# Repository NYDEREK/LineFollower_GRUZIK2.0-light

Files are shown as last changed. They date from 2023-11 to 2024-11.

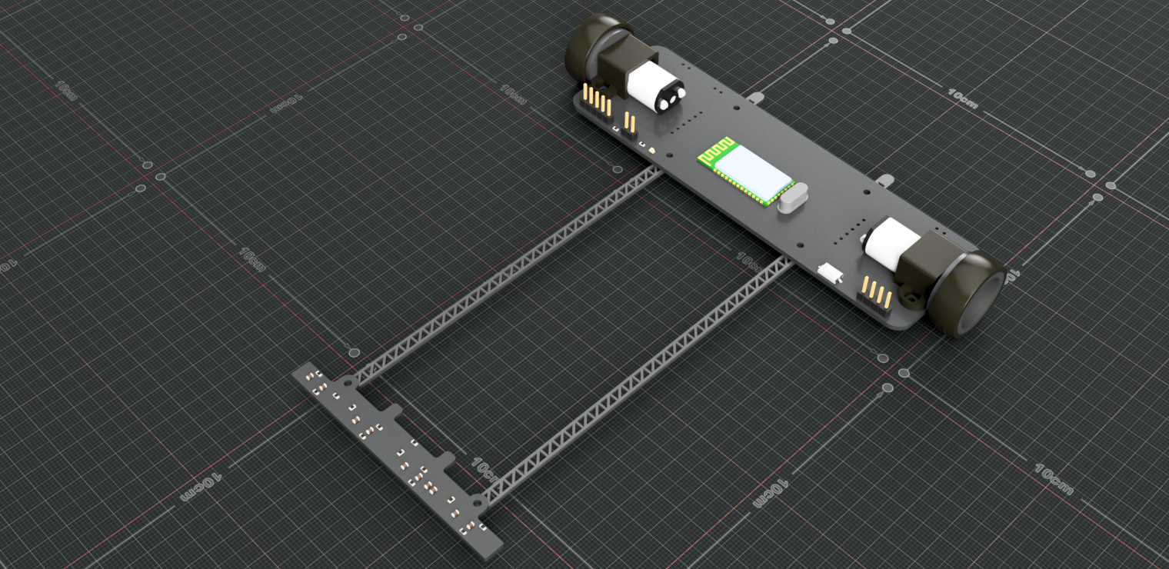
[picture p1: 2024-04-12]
Gruzik2.0-light/Hardware/CAD_Renders/Gruzik2.0_Sensor v7.png

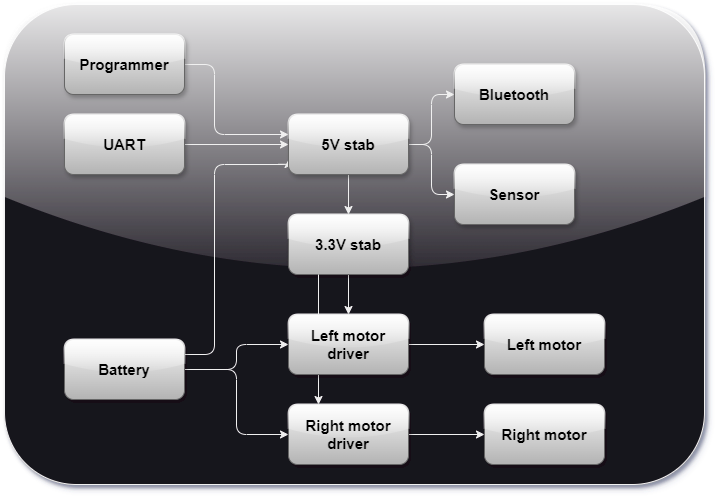
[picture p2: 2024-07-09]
Gruzik2.0-light/Hardware/SubSystem/Power_schemat.png

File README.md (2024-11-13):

<h1 align="center">GRUZIK2.0: Line Follower Robot</h1>

<div align="center">

   

<i>Loved the project? Please consider giving a Star ⭐️</i>

</div>

> **GRUZIK2.0 is a lightweight construction (62g) designed for the "Line Follower Light" competition. The robot features Bluetooth communication with a smartphone app and uses a digital sensor instead of analog.**

<div align="center">
  
</div>

<div align="center">
  
  
</div>

## Hardware

> **The simple lightweight construction (74g) allows the robot to achieve high speed on the track.**
> **PCBs were designed in KiCAD 7.0 and manufactured by JLCPCB. The rims were 3D printed with PETG for Kyosho "Mini Z" tires.**
> **The light dualsky 150mAh battery provides enough current (max 30C) without adding too much weight (10g).**
> **The Pololu 2211 motor (10:1) with max current 1.6A per one requires the use of two separate TB6612FNG motor drivers with connected channels (max 2A per driver).**
> **The HC-05 Bluetooth module gives communication range up to 10m.**
> **The fast ARM microcontroller STM32F103C8T6 (max 72MHz) provides a lot of software capabilities.**

- uC - STM32F103C8T6
- drivers - TB6612FNG
- sensor - 8x KTIR0711S
- battery - 150mAh LiPo dualsky
- wheels - Kyosho Mini Z
- motors - Pololu 2211
- Bluetooth - HC-05

<div align="center">
  
  
</div>

## 📱Bluetooth Apps 📱

> **Thease are simple Bluetooth apps created with MIT App Inventor. Spps start and stop the robot. The Modes pad is responsible for quickly adapting the speed and accuracy of the robot to the route using modes, and the application also displays the battery charge status. Second app is mainly for tweaking PID settings it allows you to change any parameter in seconds**

<div align="center">
  
  
</div>

## Credits

> <i>**I implemented the PD controller in my project, drawing inspiration from Bilal Kabas' repository available at - https://github.com/sametoguten/STM32-Line-Follower-with-PID with MIT License - [MIT License](LICENSE)**<i>

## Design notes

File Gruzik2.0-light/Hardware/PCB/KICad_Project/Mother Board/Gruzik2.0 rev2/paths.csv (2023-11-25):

Kod sieci | Nazwa sieci | Liczba pól lut | Liczba przelotek | Długość przelotki | Długość ścieżki | Długość rdzenia | Długość Sieci | F.Cu | B.Cu
001 | GND | 44 | 0 | 0,0000 mm | 0,0000 mm | 0,0000 mm | 0,0000 mm | 0,0000 mm | 0,0000 mm
002 | /BOOT0 | 3 | 0 | 0,0000 mm | 0,0000 mm | 0,0000 mm | 0,0000 mm | 0,0000 mm | 0,0000 mm
003 | +3.3V | 15 | 0 | 0,0000 mm | 0,0000 mm | 0,0000 mm | 0,0000 mm | 0,0000 mm | 0,0000 mm
004 | /HSE_OUT | 3 | 2 | 3,0900 mm | 22,3316 mm | 0,0000 mm | 25,4216 mm | 9,0906 mm | 13,2411 mm
005 | /HSE_IN | 3 | 2 | 3,0900 mm | 21,1634 mm | 0,0000 mm | 24,2534 mm | 9,8856 mm | 11,2778 mm
006 | +3.3VA | 4 | 0 | 0,0000 mm | 0,0000 mm | 0,0000 mm | 0,0000 mm | 0,0000 mm | 0,0000 mm
007 | VDC | 10 | 0 | 0,0000 mm | 0,0000 mm | 0,0000 mm | 0,0000 mm | 0,0000 mm | 0,0000 mm
008 | +5V | 14 | 0 | 0,0000 mm | 0,0000 mm | 0,0000 mm | 0,0000 mm | 0,0000 mm | 0,0000 mm
009 | Motor_R | 7 | 0 | 0,0000 mm | 0,0000 mm | 0,0000 mm | 0,0000 mm | 0,0000 mm | 0,0000 mm
010 | Motor_L | 7 | 0 | 0,0000 mm | 0,0000 mm | 0,0000 mm | 0,0000 mm | 0,0000 mm | 0,0000 mm
011 | Net-(D1-K) | 2 | 0 | 0,0000 mm | 0,0000 mm | 0,0000 mm | 0,0000 mm | 0,0000 mm | 0,0000 mm
012 | PC13 | 2 | 0 | 0,0000 mm | 0,0000 mm | 0,0000 mm | 0,0000 mm | 0,0000 mm | 0,0000 mm
013 | PB0 | 2 | 0 | 0,0000 mm | 0,0000 mm | 0,0000 mm | 0,0000 mm | 0,0000 mm | 0,0000 mm
014 | PA7 | 2 | 0 | 0,0000 mm | 0,0000 mm | 0,0000 mm | 0,0000 mm | 0,0000 mm | 0,0000 mm
015 | PA6 | 2 | 0 | 0,0000 mm | 0,0000 mm | 0,0000 mm | 0,0000 mm | 0,0000 mm | 0,0000 mm
016 | PA5 | 2 | 0 | 0,0000 mm | 0,0000 mm | 0,0000 mm | 0,0000 mm | 0,0000 mm | 0,0000 mm
017 | PA4 | 2 | 0 | 0,0000 mm | 0,0000 mm | 0,0000 mm | 0,0000 mm | 0,0000 mm | 0,0000 mm
018 | PA3 | 2 | 0 | 0,0000 mm | 0,0000 mm | 0,0000 mm | 0,0000 mm | 0,0000 mm | 0,0000 mm
019 | PA2 | 2 | 0 | 0,0000 mm | 0,0000 mm | 0,0000 mm | 0,0000 mm | 0,0000 mm | 0,0000 mm
020 | PA1 | 2 | 0 | 0,0000 mm | 0,0000 mm | 0,0000 mm | 0,0000 mm | 0,0000 mm | 0,0000 mm
021 | PA0 | 2 | 0 | 0,0000 mm | 0,0000 mm | 0,0000 mm | 0,0000 mm | 0,0000 mm | 0,0000 mm
022 | Net-(Motor-STAB-Battery-L1-B) | 2 | 0 | 0,0000 mm | 0,0000 mm | 0,0000 mm | 0,0000 mm | 0,0000 mm | 0,0000 mm
023 | Net-(Motor-STAB-Battery-R1-B) | 2 | 0 | 0,0000 mm | 0,0000 mm | 0,0000 mm | 0,0000 mm | 0,0000 mm | 0,0000 mm
024 | Net-(Motor_L1-Pin_1) | 5 | 0 | 0,0000 mm | 0,0000 mm | 0,0000 mm | 0,0000 mm | 0,0000 mm | 0,0000 mm
025 | Net-(Motor_L1-Pin_2) | 5 | 0 | 0,0000 mm | 0,0000 mm | 0,0000 mm | 0,0000 mm | 0,0000 mm | 0,0000 mm
026 | Net-(Motor_R1-Pin_1) | 5 | 0 | 0,0000 mm | 0,0000 mm | 0,0000 mm | 0,0000 mm | 0,0000 mm | 0,0000 mm
027 | Net-(Motor_R1-Pin_2) | 5 | 0 | 0,0000 mm | 0,0000 mm | 0,0000 mm | 0,0000 mm | 0,0000 mm | 0,0000 mm
028 | SWDIO | 2 | 0 | 0,0000 mm | 0,0000 mm | 0,0000 mm | 0,0000 mm | 0,0000 mm | 0,0000 mm
029 | SWCLK | 2 | 0 | 0,0000 mm | 0,0000 mm | 0,0000 mm | 0,0000 mm | 0,0000 mm | 0,0000 mm
030 | PB1 | 3 | 0 | 0,0000 mm | 0,0000 mm | 0,0000 mm | 0,0000 mm | 0,0000 mm | 0,0000 mm
031 | Net-(SW_Reset1-B) | 2 | 0 | 0,0000 mm | 0,0000 mm | 0,0000 mm | 0,0000 mm | 0,0000 mm | 0,0000 mm
032 | PC14 | 1 | 0 | 0,0000 mm | 0,0000 mm | 0,0000 mm | 0,0000 mm | 0,0000 mm | 0,0000 mm
033 | PC15 | 1 | 0 | 0,0000 mm | 0,0000 mm | 0,0000 mm | 0,0000 mm | 0,0000 mm | 0,0000 mm
034 | PB2 | 1 | 0 | 0,0000 mm | 0,0000 mm | 0,0000 mm | 0,0000 mm | 0,0000 mm | 0,0000 mm
035 | PB10 | 3 | 0 | 0,0000 mm | 0,0000 mm | 0,0000 mm | 0,0000 mm | 0,0000 mm | 0,0000 mm
036 | PB11 | 3 | 0 | 0,0000 mm | 0,0000 mm | 0,0000 mm | 0,0000 mm | 0,0000 mm | 0,0000 mm
037 | PB12 | 1 | 0 | 0,0000 mm | 0,0000 mm | 0,0000 mm | 0,0000 mm | 0,0000 mm | 0,0000 mm
038 | PB13 | 1 | 0 | 0,0000 mm | 0,0000 mm | 0,0000 mm | 0,0000 mm | 0,0000 mm | 0,0000 mm
039 | PB14 | 3 | 0 | 0,0000 mm | 0,0000 mm | 0,0000 mm | 0,0000 mm | 0,0000 mm | 0,0000 mm
040 | PB15 | 3 | 0 | 0,0000 mm | 0,0000 mm | 0,0000 mm | 0,0000 mm | 0,0000 mm | 0,0000 mm
041 | PA8 | 1 | 0 | 0,0000 mm | 0,0000 mm | 0,0000 mm | 0,0000 mm | 0,0000 mm | 0,0000 mm
042 | PA9 | 1 | 0 | 0,0000 mm | 0,0000 mm | 0,0000 mm | 0,0000 mm | 0,0000 mm | 0,0000 mm
043 | PA10 | 1 | 0 | 0,0000 mm | 0,0000 mm | 0,0000 mm | 0,0000 mm | 0,0000 mm | 0,0000 mm
044 | PA11 | 1 | 0 | 0,0000 mm | 0,0000 mm | 0,0000 mm | 0,0000 mm | 0,0000 mm | 0,0000 mm
045 | PA12 | 1 | 0 | 0,0000 mm | 0,0000 mm | 0,0000 mm | 0,0000 mm | 0,0000 mm | 0,0000 mm
046 | PA15 | 1 | 0 | 0,0000 mm | 0,0000 mm | 0,0000 mm | 0,0000 mm | 0,0000 mm | 0,0000 mm
047 | SWO | 1 | 0 | 0,0000 mm | 0,0000 mm | 0,0000 mm | 0,0000 mm | 0,0000 mm | 0,0000 mm
048 | PB4 | 3 | 0 | 0,0000 mm | 0,0000 mm | 0,0000 mm | 0,0000 mm | 0,0000 mm | 0,0000 mm
049 | PB5 | 3 | 0 | 0,0000 mm | 0,0000 mm | 0,0000 mm | 0,0000 mm | 0,0000 mm | 0,0000 mm
050 | PB6 | 3 | 0 | 0,0000 mm | 0,0000 mm | 0,0000 mm | 0,0000 mm | 0,0000 mm | 0,0000 mm
051 | PB7 | 3 | 0 | 0,0000 mm | 0,0000 mm | 0,0000 mm | 0,0000 mm | 0,0000 mm | 0,0000 mm
052 | PB8 | 1 | 0 | 0,0000 mm | 0,0000 mm | 0,0000 mm | 0,0000 mm | 0,0000 mm | 0,0000 mm
053 | PB9 | 3 | 0 | 0,0000 mm | 0,0000 mm | 0,0000 mm | 0,0000 mm | 0,0000 mm | 0,0000 mm
056 | Net-(U4-PGND1-Pad3) | 4 | 0 | 0,0000 mm | 0,0000 mm | 0,0000 mm | 0,0000 mm | 0,0000 mm | 0,0000 mm
057 | Net-(U5-PGND1-Pad3) | 4 | 0 | 0,0000 mm | 0,0000 mm | 0,0000 mm | 0,0000 mm | 0,0000 mm | 0,0000 mm

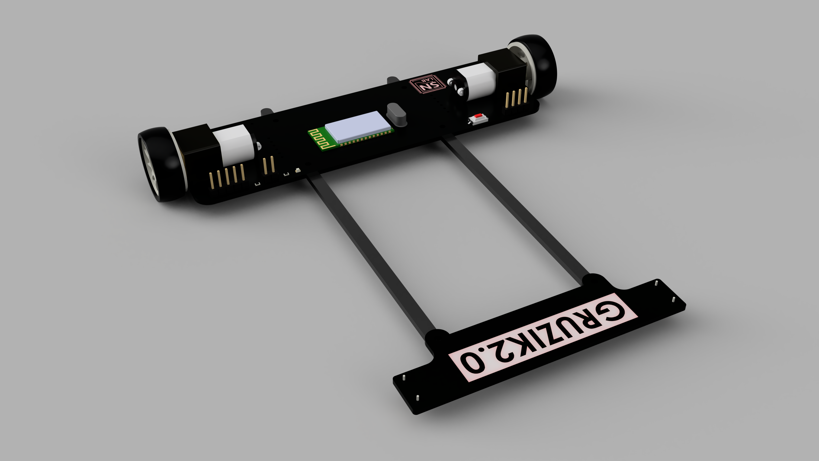
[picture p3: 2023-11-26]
Gruzik2.0-light/Hardware/CAD_Renders/26.11.2023r-First_render.PNG

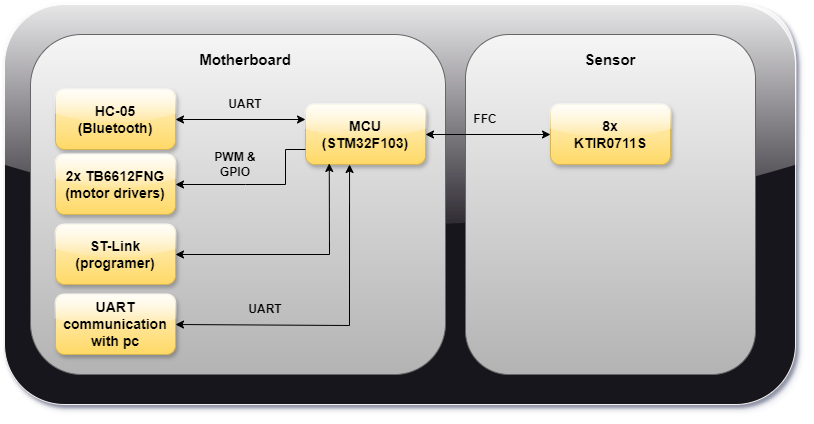
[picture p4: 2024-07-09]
Gruzik2.0-light/Hardware/SubSystem/signals.png

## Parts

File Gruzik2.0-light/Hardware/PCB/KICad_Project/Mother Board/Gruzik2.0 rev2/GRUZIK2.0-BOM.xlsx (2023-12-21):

Nr | Reference | Qty | Val | Footprint | SOURCE
 | MAIN BOARD
1 | BOOT1 | 1 | - | Conn_PinHeader_2.54mm_1x02 | HOME
2 | C1 | 1 | 4u7 | SMD 0603 1608metric | LCSC
3 | C2,C4,C6,C7,C9,C20 | 6 | 100n | SMD 0603 1608metric | LCSC
4 | C3,C5 | 2 | 20p | SMD 0603 1608metric | LCSC
5 | C8 | 1 | 1u | SMD 0603 1608metric | LCSC
6 | C10,C12,C16,C19 | 4 | 10u | SMD 0603 1608metric | LCSC
7 | C11,C13 | 2 | 33u -> 22u | SMD 0603 1608metric | LCSC
8 | C14,C15,C17,C18 | 5 | 0.1u | SMD 0603 1608metric | LCSC
9 | D1 | 1 | Blue | LED_0603_1608metric | LCSC
10 | Conn-FFC | 2 |  | 01x16-1.0mm grid -Druciarstwo z footprintem | LCSC
11 | L1 | 1 | 27n | SMD 0603 1608metric | LCSC
12 | R1 | 1 | 10k | SMD 0603 1608metric | LCSC
13 | R2 | 1 | 20k | SMD 0603 1608metric | LCSC
14 | R3 | 1 | 510R | SMD 0603 1608metric | LCSC
15 | R4 | 1 | 33k | SMD 0603 1608metric | LCSC
16 | RESET-button | 1 | - | Button_Switch_SMD:SW_SPST_CK_RS282G05A | LCSC
17 | STM32F103C8T6 | 1 | - | LQFP-48_7x7mm_P0.5mm | LCSC
18 | LM1117MP-3,3V | 1 | - | TO_SOT_SMD:SOT-223-3_TabPin2 | LCSC
19 | LM1117MP-5V | 1 | - | TO_SOT_SMD:SOT-223-3_TabPin2 | LCSC
20 | TB6612FNG | 2 |  | SSOP-24_5.3x8.2mm_P0.65mm | LCSC
21 | HC-05 | 1 |  |  | HOME
22 | Crystal | 1 | 8Mhz | Crystal_HC49-4H_Vertical | LCSC
 | SENSOR
23 | C2 | 1 | 1.0u | SMD 0603 1608metric | LCSC
24 | C3, C4, C5, C6, C7, C8, C9, C10 | 8 | 10n | SMD 0603 1608metric | LCSC
25 | KTIR0711S | 8 | - | - | LCSC
26 | Q1-NMOS | 1 |  | SOT23 | LCSC
27 | R1,R4,R7,R10 | 4 | 39 | SMD 0603 1608metric | LCSC
28 | R2,R3,R5,R7,R11,R12 | 8 | 220 | SMD 0603 1608metric | LCSC
29 | R12,R14 | 2 | 47 | SMD 0603 1608metric | LCSC
30 | R15 | 1 | 47K | SMD 0603 1608metric | LCSC

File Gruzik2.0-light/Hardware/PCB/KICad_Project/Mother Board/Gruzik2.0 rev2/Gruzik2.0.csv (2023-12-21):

# | Reference | Qty | Value | Footprint | DNP
1 | BOOT1 | 1 | Conn_01x02_Pin | Connector_PinHeader_2.54mm:PinHeader_1x02_P2.54mm_Vertical
2 | C1 | 1 | 4u7 | Capacitor_SMD:C_0603_1608Metric
3 | C2, C4, C6, C7, C9, C20 | 6 | 100n | Capacitor_SMD:C_0603_1608Metric
4 | C3, C5 | 2 | 20p | Capacitor_SMD:C_0603_1608Metric
5 | C8 | 1 | 1u | Capacitor_SMD:C_0603_1608Metric
6 | C10, C12, C16, C19 | 4 | 10u | Capacitor_SMD:C_0603_1608Metric
7 | C11, C13 | 2 | 33u | Capacitor_SMD:C_0603_1608Metric
8 | C14, C15, C17, C18 | 4 | 0.1u | Capacitor_SMD:C_0603_1608Metric
9 | D1 | 1 | BLUE | LED_SMD:LED_0603_1608Metric
10 | GRUZIK2.0 | 1 | Conn_01x16 | Connector_FFC-FPC:Molex_200528-0160_1x16-1MP_P1.00mm_Horizontal
11 | L1 | 1 | 27n | Inductor_SMD:L_0603_1608Metric
12 | Motor-Battery_L1, Motor-Battery_R1, Motor-STAB-Battery-L1, Motor-STAB-Battery-R1 | 4 | SolderJumper_2_Open | Jumper:SolderJumper-2_P1.3mm_Open_RoundedPad1.0x1.5mm
13 | MOTOR_L1, MOTOR_R1 | 2 | Conn_01x02 | Connector_PinHeader_2.54mm:PinHeader_1x02_P2.54mm_Vertical
14 | PROG1 | 1 | Conn_01x05 | Connector_PinHeader_2.54mm:PinHeader_1x05_P2.54mm_Vertical
15 | R1 | 1 | 10k | Resistor_SMD:R_0603_1608Metric
16 | R2 | 1 | 20K | Resistor_SMD:R_0603_1608Metric
17 | R3 | 1 | 510R | Resistor_SMD:R_0603_1608Metric
18 | R4 | 1 | 33K | Resistor_SMD:R_0603_1608Metric
19 | RESET1 | 1 | SW_SPST | Button_Switch_SMD:SW_SPST_CK_RS282G05A3
20 | U1 | 1 | STM32F103C8T6 | Package_QFP:LQFP-48_7x7mm_P0.5mm
21 | U2 | 1 | LM1117MP-3.3 | Package_TO_SOT_SMD:SOT-223-3_TabPin2
22 | U3 | 1 | LM1117MP-5.0 | Package_TO_SOT_SMD:SOT-223-3_TabPin2
23 | U3V40F7-POLOLU1, U3V40F7-POLOLU2 | 2 | Conn_01x06 | Connector_PinSocket_2.54mm:PinSocket_1x06_P2.54mm_Vertical
24 | U4, U5 | 2 | TB6612FNG | Package_SO:SSOP-24_5.3x8.2mm_P0.65mm
25 | U7 | 1 | HC-05 | HC-05_module:XCVR_HC-05
26 | UART1 | 1 | Conn_01x04 | Connector_PinHeader_2.54mm:PinHeader_1x04_P2.54mm_Vertical
27 | VIN1 | 1 | Conn_01x02 | Connector_PinSocket_2.54mm:PinSocket_1x02_P2.54mm_Vertical
28 | Y1 | 1 | 8MHz | Crystal:Crystal_HC49-4H_Vertical

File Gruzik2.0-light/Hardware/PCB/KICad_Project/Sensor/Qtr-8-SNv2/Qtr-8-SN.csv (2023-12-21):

# | Reference | Qty | Value | Footprint | DNP
1 | C1 | 1 | 0.1u | Capacitor_SMD:C_0603_1608Metric
2 | C2 | 1 | 1.0u | Capacitor_SMD:C_0603_1608Metric
3 | C3, C4, C5, C6, C7, C8, C9, C10 | 8 | 10n | Capacitor_SMD:C_0603_1608Metric
4 | IC1, IC2, IC3, IC4, IC5, IC6, IC7, IC8 | 8 | ~ | Sensor_Optical:KTIR0711S
5 | Q1 | 1 | NMOS | NMOS_new:NMOS_SN
6 | R1, R4, R7, R10 | 4 | 39 | Resistor_SMD:R_0603_1608Metric
7 | R2, R3, R5, R6, R8, R9, R11, R12 | 8 | 220 | Resistor_SMD:R_0603_1608Metric
8 | R13, R14 | 2 | 47 | Resistor_SMD:R_0603_1608Metric
9 | R15 | 1 | 47K | Resistor_SMD:R_0603_1608Metric
10 | R16, R17 | 2 | R | Resistor_THT:R_Axial_DIN0207_L6.3mm_D2.5mm_P7.62mm_Horizontal
11 | Sensor1 | 1 | Conn_01x16 | Connector_FFC-FPC:Molex_200528-0160_1x16-1MP_P1.00mm_Horizontal

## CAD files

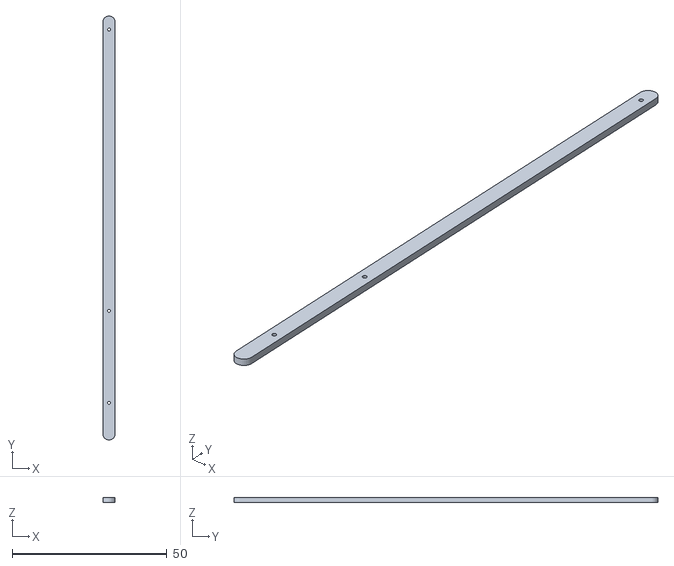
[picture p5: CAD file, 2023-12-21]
Gruzik2.0-light/Hardware/3D_printed_frame/Frame_thinner.stl
4.00 x 136.9 x 1.50

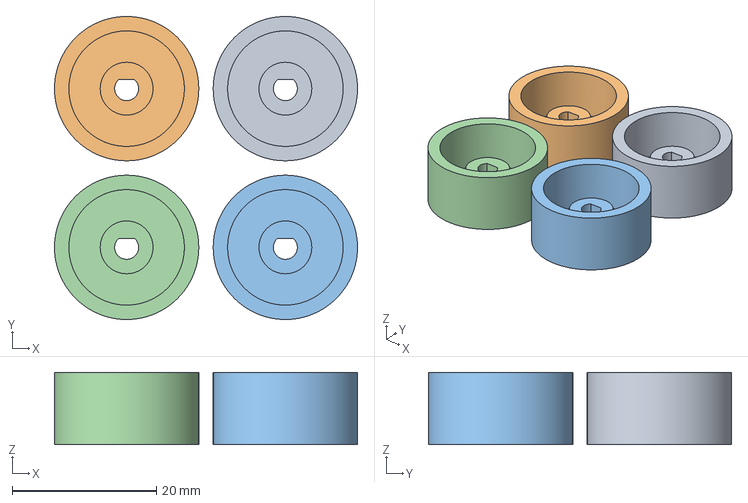
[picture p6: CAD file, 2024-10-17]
Gruzik2.0-light/Hardware/3D_Printed_Parts/LF_wheel_2.1_design.3mf
42.0 x 42.0 x 10.0 mm
LF_wheel.stl x 4

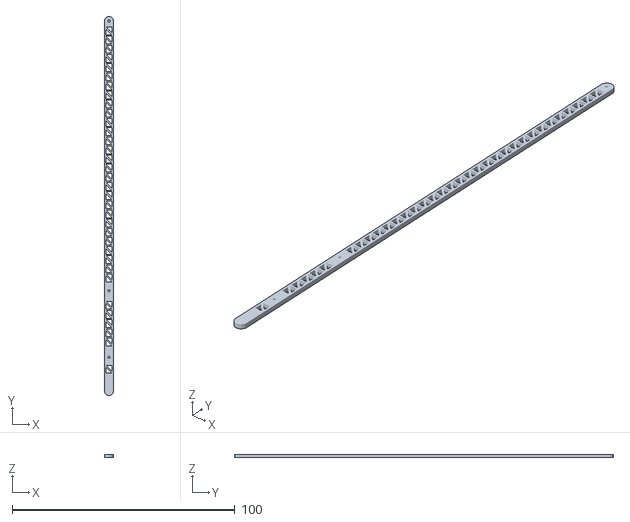
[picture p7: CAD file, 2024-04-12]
Gruzik2.0-light/Hardware/3D_Printed_Parts/Longer Version/Frame_1.stl
4.00 x 170.0 x 1.50

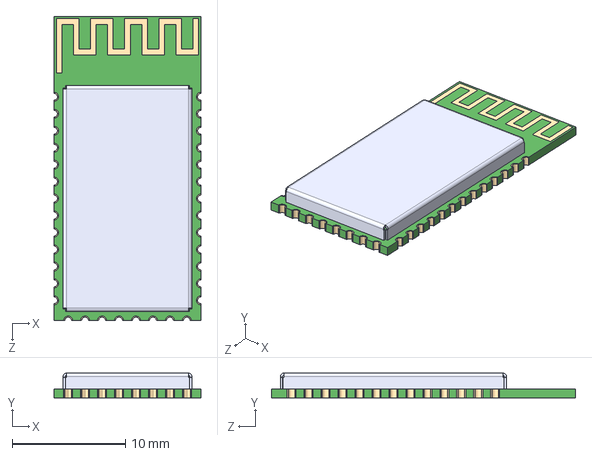
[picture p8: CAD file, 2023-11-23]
Gruzik2.0-light/Hardware/PCB/KICad_Project/Mother Board/Gruzik2.0 rev2/HC-05/HC-05.step
13.0 x 2.20 x 26.9 mm

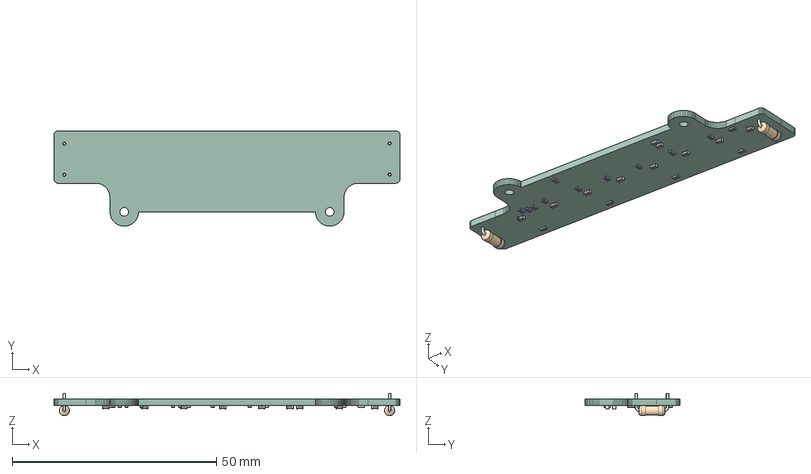
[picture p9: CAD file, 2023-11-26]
Gruzik2.0-light/Hardware/PCB/STEP_Files/Qtr-8-SN.step
84.7 x 23.3 x 5.50 mm
PCB

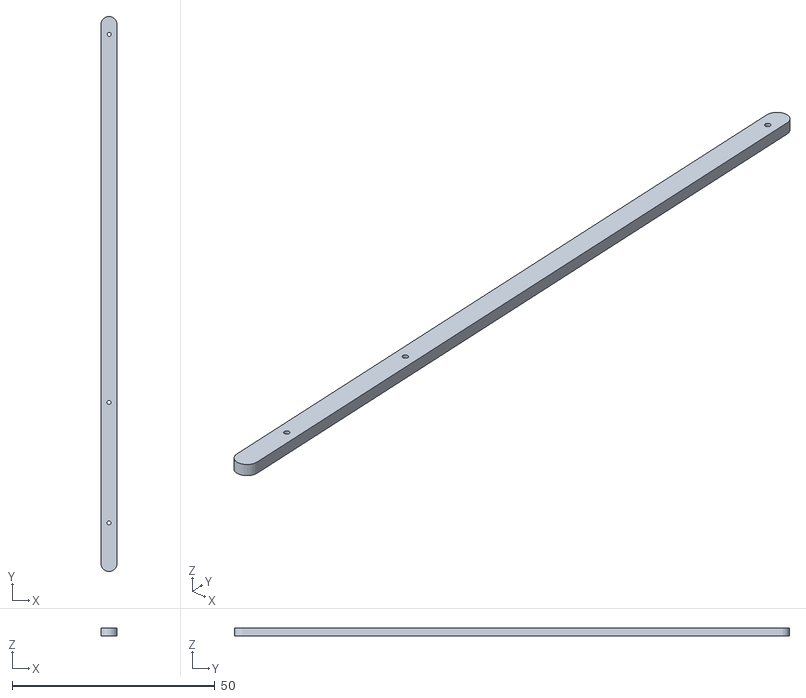
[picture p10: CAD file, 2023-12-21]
Gruzik2.0-light/Hardware/3D_printed_frame/GRUZIK2.0_Frame_Part.stl
4.00 x 136.9 x 2.00

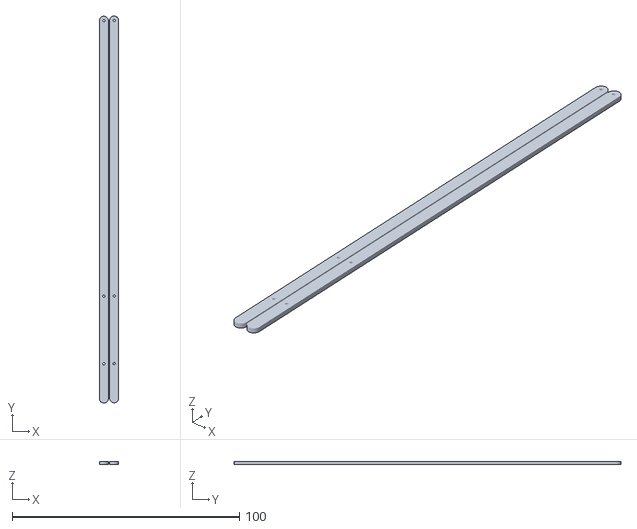
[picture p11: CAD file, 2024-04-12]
Gruzik2.0-light/Hardware/3D_Printed_Parts/Longer Version/Frame_2.stl
8.54 x 170.1 x 1.50

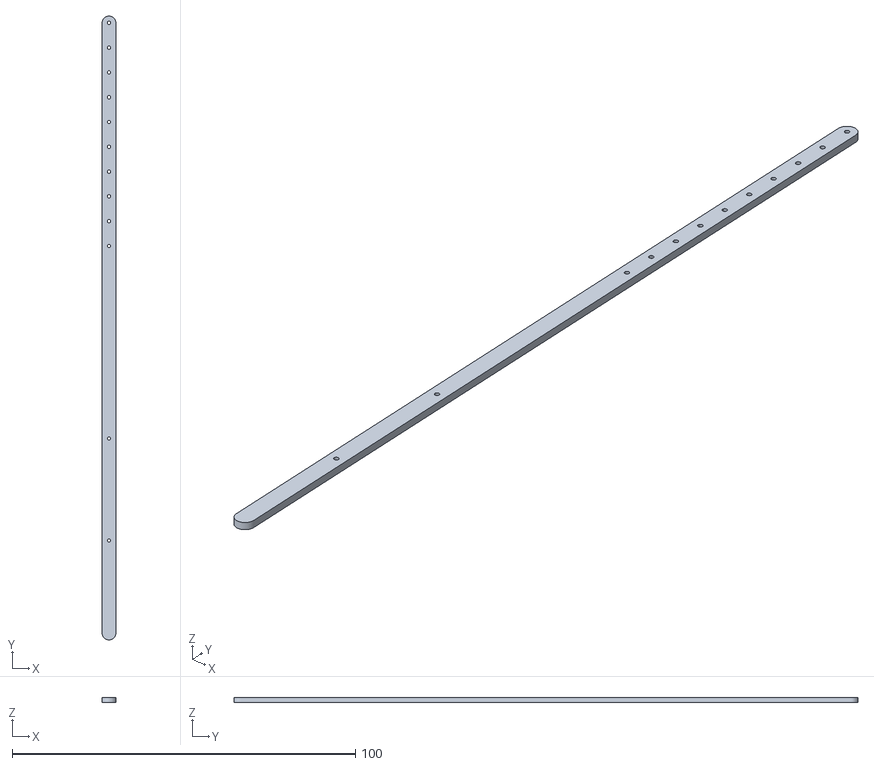
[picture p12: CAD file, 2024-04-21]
Gruzik2.0-light/Hardware/3D_Printed_Parts/mount.stl
4.00 x 181.8 x 1.50

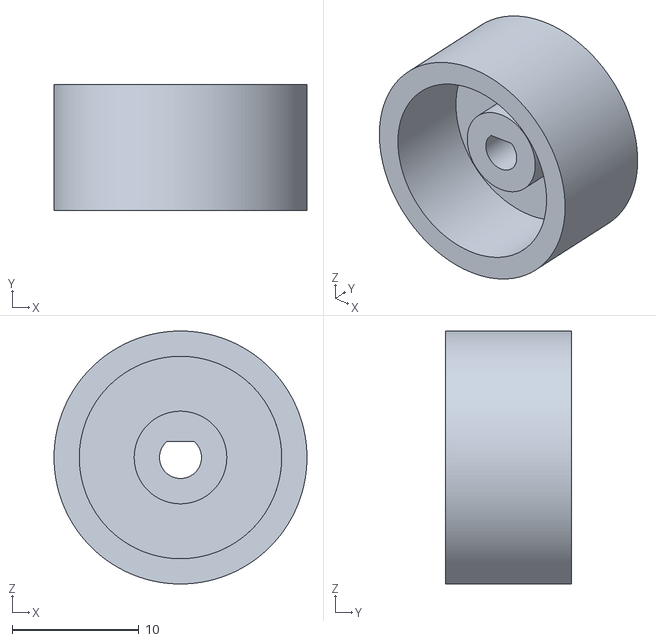
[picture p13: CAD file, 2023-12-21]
Gruzik2.0-light/Hardware/3D_Printed_Parts/LF_wheel.stl
20.0 x 10.0 x 20.0

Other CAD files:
Gruzik2.0-light/Hardware/CAD_Models/Gruzik2.0 v16.f3d

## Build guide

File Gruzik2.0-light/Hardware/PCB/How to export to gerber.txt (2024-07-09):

https://www.youtube.com/watch?v=n5wi2HQm2WA

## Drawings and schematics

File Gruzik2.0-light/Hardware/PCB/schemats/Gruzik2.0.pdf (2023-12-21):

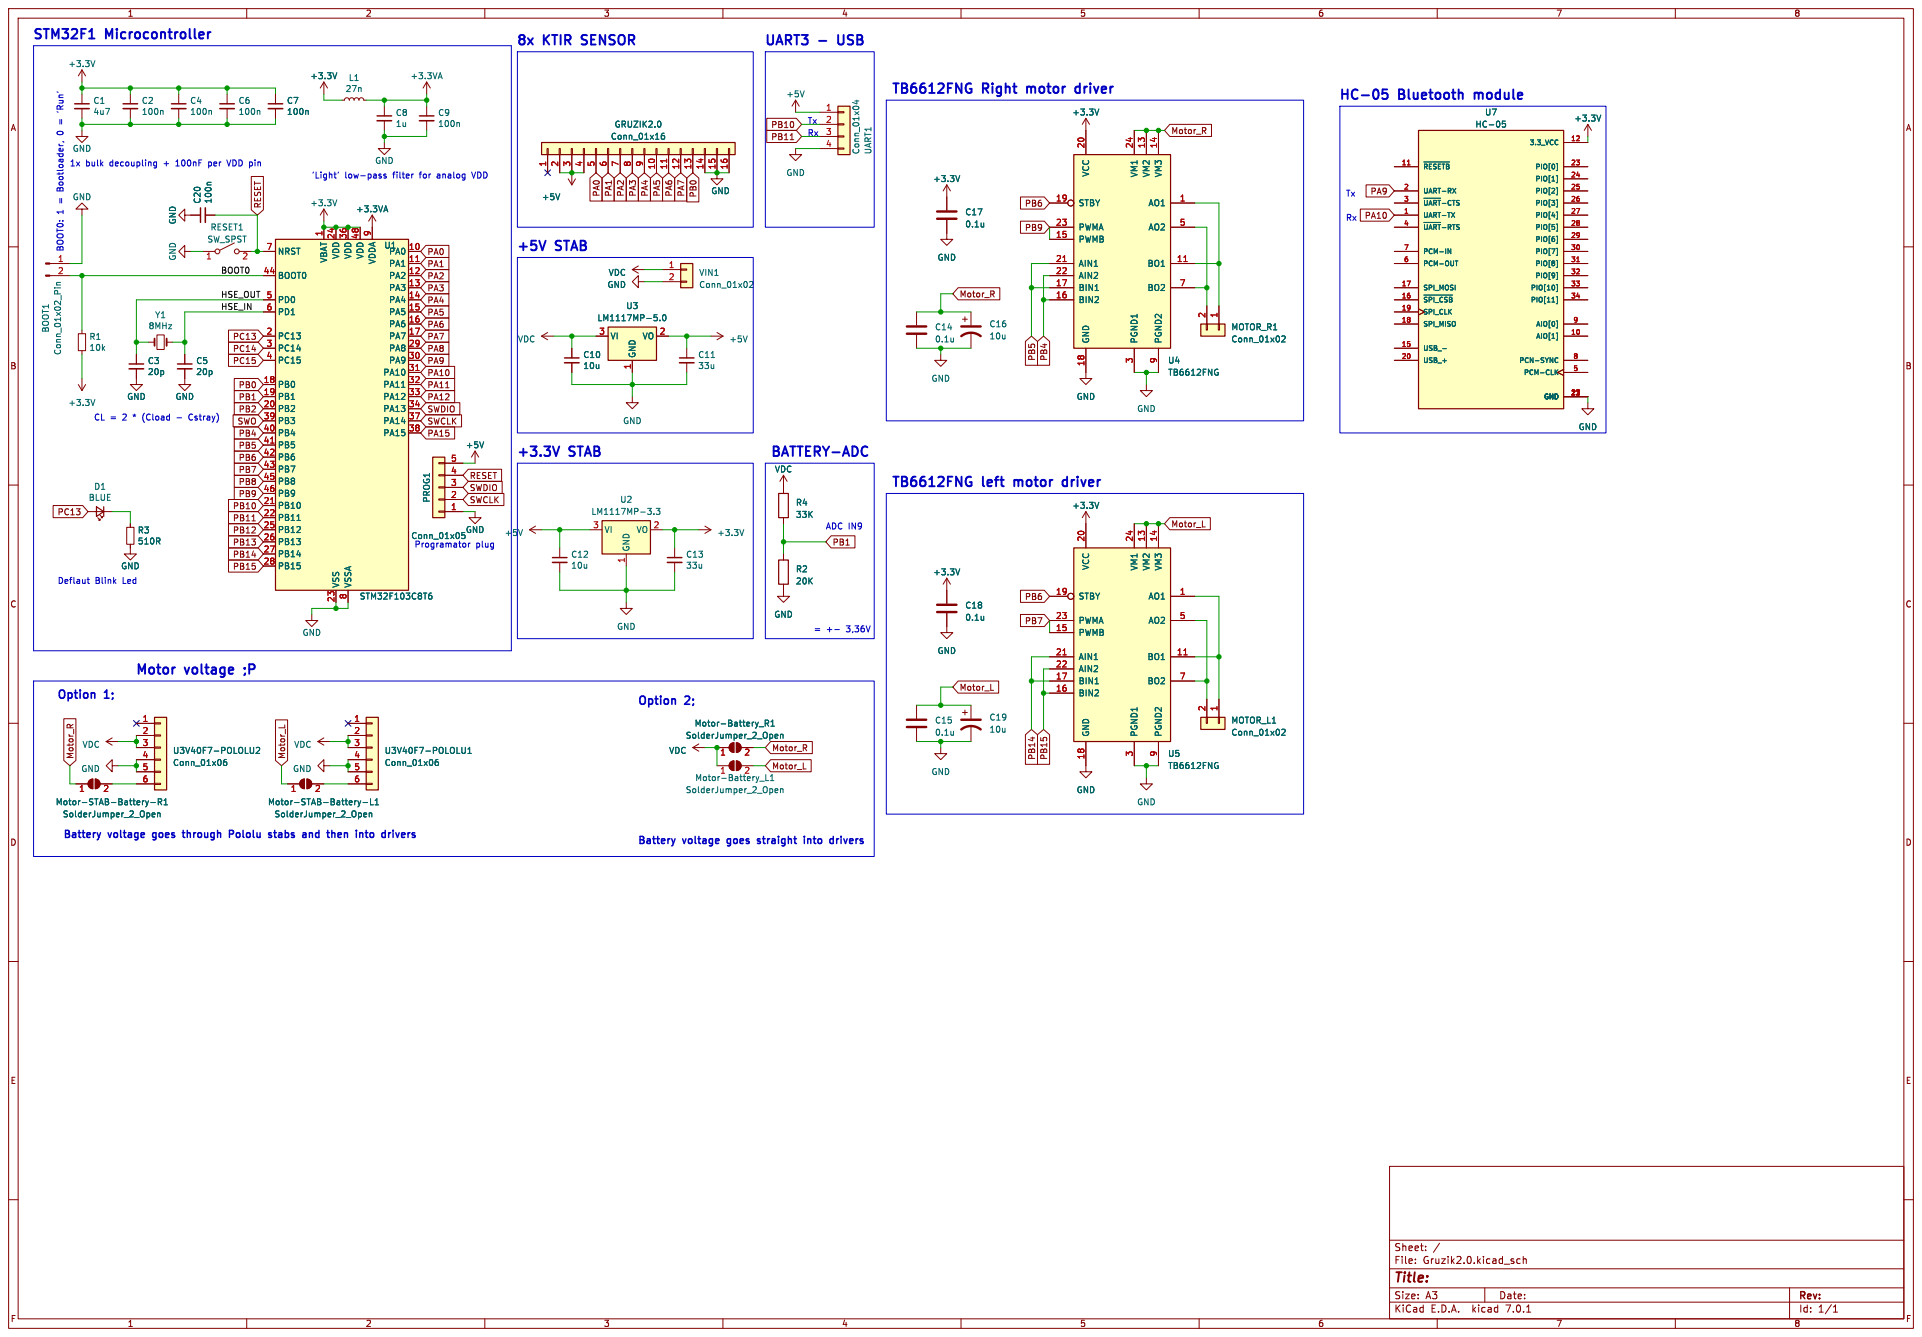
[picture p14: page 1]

1 MOTOR_R1 Conn_01x02 AO1 1 BO1 11 VM2 13 VM3 14 PWMB 15 BIN2 16 BIN1 17 GND 18 STBY 19 VCC 20 AIN1 21 AIN2 22 PWMA 23 VM1 24 PGND1

Rx TB6612FNG left motor driver

1 PA0 10 PA1 11 PA2 12 PA3 13 PA4 14 PA5 15 PA6 16 PA7 17 PB0 18 PB1 19 PC13 2 PB2 20 PB10 21 PB11 22 VSS 23 VDD 24 PB12 25 PB13 26 PB14 27 PB15 28 PA8 29 PC14 3 PA9 30 PA10 31 PA11 32 PA12 33 PA13 34 VDD 36 PA14 37 PA15 38 PB3 39 PC15 4 PB4 40 PB5 41 PB6 42 PB7 43 BOOT0 44 PB8 45 PB9 46 VDD 48 PD0 5 PD1 6 NRST 7 VSSA

6 Motor-STAB-Battery-R1
SolderJumper_2_Open
Battery voltage goes through Pololu stabs and then into drivers

Battery voltage goes straight into drivers

Id: 1/1 Title: File: Gruzik2.0.kicad_sch Sheet: /

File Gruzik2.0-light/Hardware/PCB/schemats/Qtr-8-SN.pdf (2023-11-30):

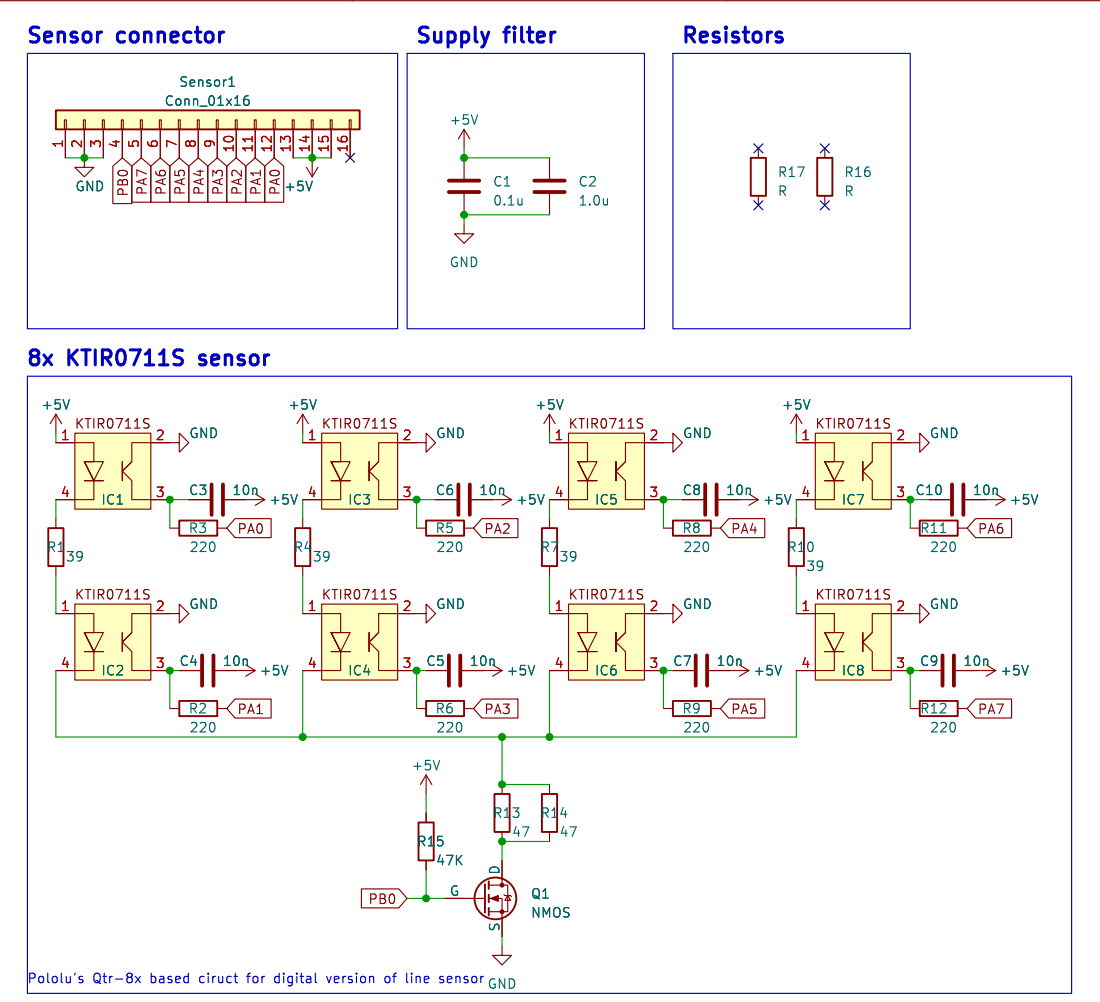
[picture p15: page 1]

Id: 1/1 Title: File: Qtr-8-SN.kicad_sch Sheet: /

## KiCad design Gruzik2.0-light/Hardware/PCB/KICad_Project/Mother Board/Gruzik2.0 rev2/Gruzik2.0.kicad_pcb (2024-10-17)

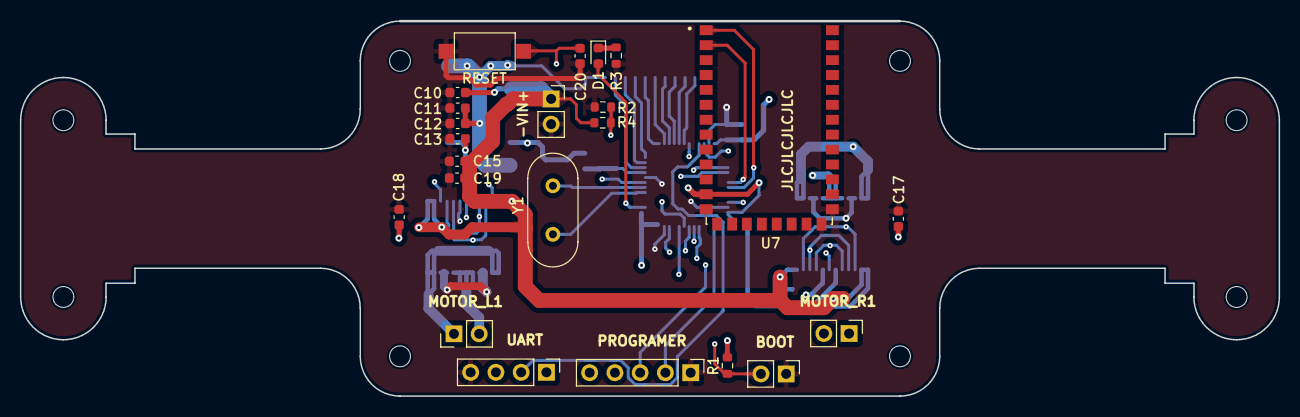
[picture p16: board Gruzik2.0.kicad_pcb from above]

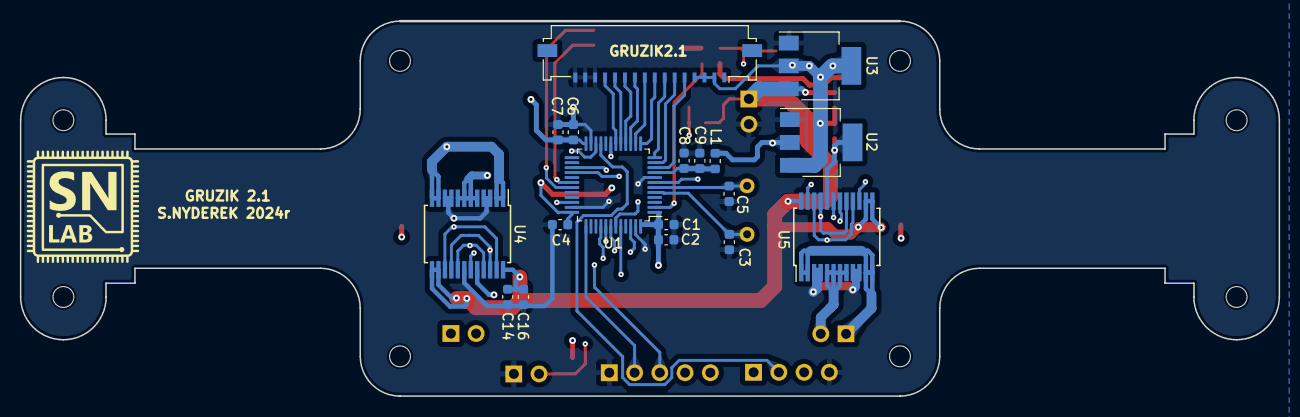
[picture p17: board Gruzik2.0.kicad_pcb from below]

Board: 4 copper layers, 126.6 x 37.7 mm, 41 parts (18 on the bottom side), 38 nets.

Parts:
-VIN+: Conn_01x02; PinSocket_1x02_P2.54mm_Vertical
BOOT: Conn_01x02_Pin; PinHeader_1x02_P2.54mm_Vertical
C1: 4u7; C_0603_1608Metric
C2, C4, C6, C7, C9, C20: 100n; C_0603_1608Metric
C3, C5: 20p; C_0603_1608Metric
C8: 1u; C_0603_1608Metric
C10, C12, C16, C19: 10u; C_0603_1608Metric
C11, C13: 33u; C_0603_1608Metric
C14, C15, C17, C18: 0.1u; C_0603_1608Metric
D1: BLUE; LED_0603_1608Metric
GRUZIK2.1: Conn_01x16; Molex_200528-0160_1x16-1MP_P1.00mm_Horizontal
L1: 27n; L_0603_1608Metric
MOTOR_L1: Conn_01x02; PinHeader_1x02_P2.54mm_Vertical
MOTOR_R1: Conn_01x02; PinHeader_1x02_P2.54mm_Vertical
PROGRAMER: Conn_01x05; PinHeader_1x05_P2.54mm_Vertical
R1: 10k; R_0603_1608Metric
R2: 20K; R_0603_1608Metric
R3: 510R; R_0603_1608Metric
R4: 33K; R_0603_1608Metric
RESET: SW_SPST; SW_SPST_CK_RS282G05A3
U1: STM32F103C8T6; LQFP-48_7x7mm_P0.5mm
U2: LM1117MP-3.3; SOT-223-3_TabPin2
U3: LM1117MP-5.0; SOT-223-3_TabPin2
U4, U5: TB6612FNG; SSOP-24_5.3x8.2mm_P0.65mm
U7: HC-05; XCVR_HC-05
UART: Conn_01x04; PinHeader_1x04_P2.54mm_Vertical
Y1: 8MHz; Crystal_HC49-4H_Vertical

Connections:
+3.3V: C1.1, C2.1, C4.1, C6.1, C7.1, C13.1, C17.1, C18.1, L1.1, R1.2, U1.1 (VBAT), U1.24 (VDD), U1.36 (VDD), U1.48 (VDD), U2.2 (VO), U4.20 (VCC), U5.20 (VCC), U7.12 (3.3_VCC)
+3.3VA: C8.1, C9.1, L1.2, U1.9 (VDDA)
+5V: C11.1, C12.1, GRUZIK2.1.2, GRUZIK2.1.3, GRUZIK2.1.4, PROGRAMER.5, U2.3 (VI), U3.2 (VO), UART.1
/BOOT0: BOOT.2, R1.1, U1.44 (BOOT0)
/HSE_IN: C5.1, U1.6 (PD1), Y1.2
/HSE_OUT: C3.1, U1.5 (PD0), Y1.1
GND: -VIN+.2, BOOT.1, C1.2, C2.2, C3.2, C4.2, C5.2, C6.2, C7.2, C8.2, C9.2, C10.2, C11.2, C12.2, C13.2, C14.2, C15.2, C16.2, C17.2, C18.2, C19.2, C20.1, GRUZIK2.1.14, GRUZIK2.1.15, GRUZIK2.1.16, PROGRAMER.1, R2.2, R3.2, RESET.1 (A), U1.8 (VSSA), U1.23 (VSS), U1.35 (VSS), U1.47 (VSS), U2.1 (GND), U3.1 (GND), U4.3 (PGND1), U4.4 (PGND1), U4.9 (PGND2), U4.10 (PGND2), U4.18 (GND), U5.3 (PGND1), U5.4 (PGND1), U5.9 (PGND2), U5.10 (PGND2), U5.18 (GND), U7.13 (GND), U7.21 (GND), U7.22 (GND), UART.4
unnamed: D1.1 (K), R3.1
unnamed: MOTOR_L1.1, U5.1 (AO1), U5.2 (AO1), U5.11 (BO1), U5.12 (BO1)
unnamed: MOTOR_L1.2, U5.5 (AO2), U5.6 (AO2), U5.7 (BO2), U5.8 (BO2)
unnamed: MOTOR_R1.1, U4.1 (AO1), U4.2 (AO1), U4.11 (BO1), U4.12 (BO1)
unnamed: MOTOR_R1.2, U4.5 (AO2), U4.6 (AO2), U4.7 (BO2), U4.8 (BO2)
PA0: GRUZIK2.1.5, U1.10 (PA0)
PA1: GRUZIK2.1.6, U1.11 (PA1)
PA2: GRUZIK2.1.7, U1.12 (PA2)
PA3: GRUZIK2.1.8, U1.13 (PA3)
PA4: GRUZIK2.1.9, U1.14 (PA4)
PA5: GRUZIK2.1.10, U1.15 (PA5)
PA6: GRUZIK2.1.11, U1.16 (PA6)
PA7: GRUZIK2.1.12, U1.17 (PA7)
PA9: U1.30 (PA9), U7.2 (UART-RX)
PA10: U1.31 (PA10), U7.1 (UART-TX)
PB0: GRUZIK2.1.13, U1.18 (PB0)
PB1: R2.1, R4.1, U1.19 (PB1)
PB4: U1.40 (PB4), U4.16 (BIN2), U4.22 (AIN2)
PB5: U1.41 (PB5), U4.17 (BIN1), U4.21 (AIN1)
PB6: U1.42 (PB6), U4.19 (STBY), U5.19 (STBY)
PB7: U1.43 (PB7), U5.15 (PWMB), U5.23 (PWMA)
PB9: U1.46 (PB9), U4.15 (PWMB), U4.23 (PWMA)
PB10: U1.21 (PB10), UART.2
PB11: U1.22 (PB11), UART.3
PB14: U1.27 (PB14), U5.17 (BIN1), U5.21 (AIN1)
PB15: U1.28 (PB15), U5.16 (BIN2), U5.22 (AIN2)
PC13: D1.2 (A), U1.2 (PC13)
RESET: C20.2, PROGRAMER.4, RESET.2 (B), U1.7 (NRST)
SWCLK: PROGRAMER.2, U1.37 (PA14)
SWDIO: PROGRAMER.3, U1.34 (PA13)
VDC: -VIN+.1, C10.1, C14.1, C15.1, C16.1, C19.1, R4.2, U3.3 (VI), U4.13 (VM2), U4.14 (VM3), U4.24 (VM1), U5.13 (VM2), U5.14 (VM3), U5.24 (VM1)

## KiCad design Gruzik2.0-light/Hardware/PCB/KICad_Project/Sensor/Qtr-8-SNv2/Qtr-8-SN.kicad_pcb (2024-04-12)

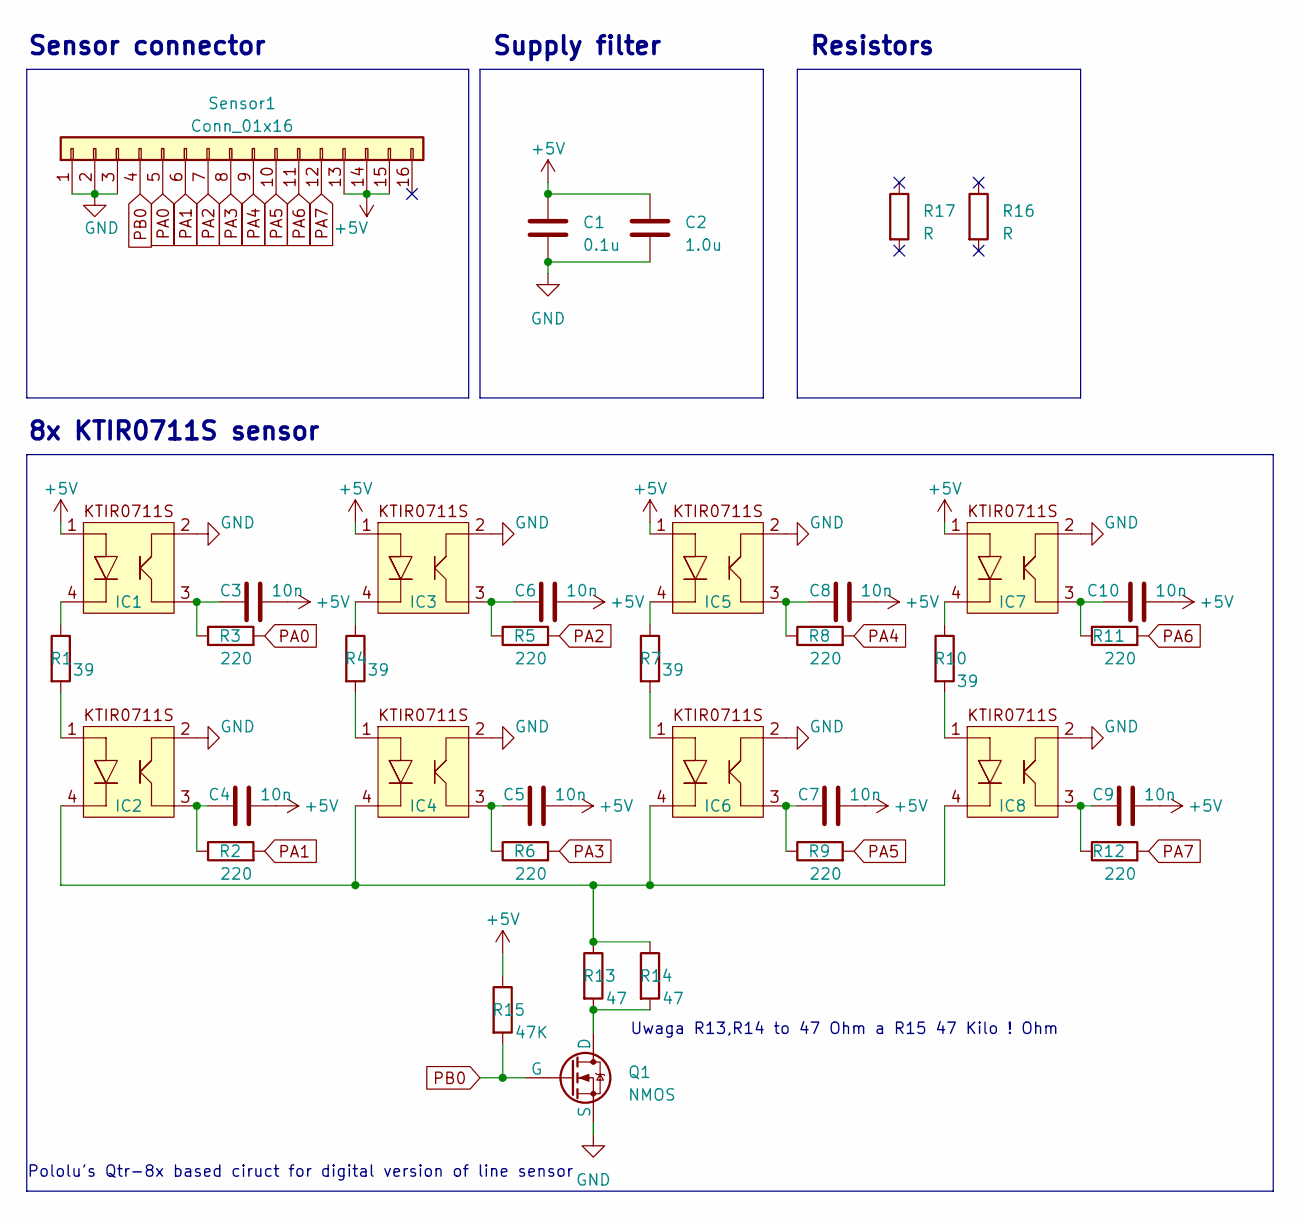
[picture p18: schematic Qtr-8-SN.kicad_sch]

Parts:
C1: 0.1u; C_0603_1608Metric
C2: 1.0u; C_0603_1608Metric
C3, C4, C5, C6, C7, C8, C9, C10: 10n; C_0603_1608Metric
IC1, IC2, IC3, IC4, IC5, IC6, IC7, IC8: KTIR0711S
Q1: NMOS; NMOS_SN
R1, R4, R7, R10: 39; R_0603_1608Metric
R2, R3, R5, R6, R8, R9, R11, R12: 220; R_0603_1608Metric
R13, R14: 47; R_0603_1608Metric
R15: 47K; R_0603_1608Metric
R16, R17: R; R_Axial_DIN0207_L6.3mm_D2.5mm_P7.62mm_Horizontal
Sensor1: Conn_01x16; Molex_200528-0160_1x16-1MP_P1.00mm_Horizontal

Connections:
+5V: C1.1, C2.1, C3.2, C4.2, C5.2, C6.2, C7.2, C8.2, C9.2, C10.2, IC1.1, IC3.1, IC5.1, IC7.1, R15.1, Sensor1.13, Sensor1.14, Sensor1.15; also elsewhere on the board
GND: C1.2, C2.2, IC1.2, IC2.2, IC3.2, IC4.2, IC5.2, IC6.2, IC7.2, IC8.2, Q1.3 (S), Sensor1.1, Sensor1.2, Sensor1.3; also elsewhere on the board
unnamed: C3.1, IC1.3, R3.1
unnamed: C4.1, IC2.3, R2.1
unnamed: C5.1, IC4.3, R6.1
unnamed: C6.1, IC3.3, R5.1
unnamed: C7.1, IC6.3, R9.1
unnamed: C8.1, IC5.3, R8.1
unnamed: C9.1, IC8.3, R12.1
unnamed: C10.1, IC7.3, R11.1
unnamed: IC1.4, R1.1
unnamed: IC2.1, R1.2
unnamed: IC2.4, IC4.4, IC6.4, IC8.4, R13.1, R14.1
unnamed: IC3.4, R4.1
unnamed: IC4.1, R4.2
unnamed: IC5.4, R7.1
unnamed: IC6.1, R7.2
unnamed: IC7.4, R10.1
unnamed: IC8.1, R10.2
unnamed: Q1.1 (D), R13.2, R14.2
PA0: R3.2, Sensor1.5; also elsewhere on the board
PA1: R2.2, Sensor1.6; also elsewhere on the board
PA2: R5.2, Sensor1.7; also elsewhere on the board
PA3: R6.2, Sensor1.8; also elsewhere on the board
PA4: R8.2, Sensor1.9; also elsewhere on the board
PA5: R9.2, Sensor1.10; also elsewhere on the board
PA6: R11.2, Sensor1.11; also elsewhere on the board
PA7: R12.2, Sensor1.12; also elsewhere on the board
PB0: Q1.2 (G), R15.2, Sensor1.4; also elsewhere on the board

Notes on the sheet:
Uwaga R13,R14 to 47 Ohm a R15 47 Kilo ! Ohm
Sensor connector
8x KTIR0711S sensor
Supply filter
Resistors
Pololu's Qtr-8x based ciruct for digital version of line sensor

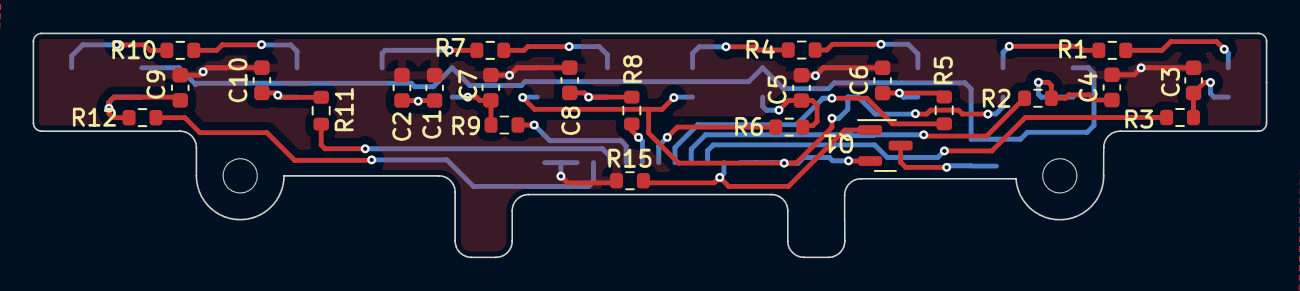
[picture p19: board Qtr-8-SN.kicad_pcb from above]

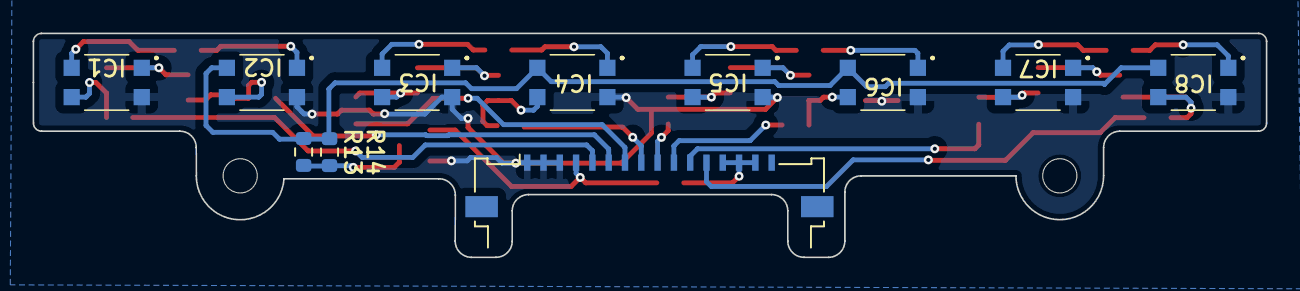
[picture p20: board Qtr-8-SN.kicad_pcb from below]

Board: 2 copper layers, 75.7 x 13.7 mm, 35 parts (11 on the bottom side), 29 nets.

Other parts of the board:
Sensor: Conn_01x16; Molex_200528-0160_1x16-1MP_P1.00mm_Horizontal

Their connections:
+5V: Sensor.13, Sensor.14, Sensor.15; also elsewhere on the board
GND: Sensor.1, Sensor.2, Sensor.3; also elsewhere on the board
PA0: Sensor.5; also elsewhere on the board
PA1: Sensor.6; also elsewhere on the board
PA2: Sensor.7; also elsewhere on the board
PA3: Sensor.8; also elsewhere on the board
PA4: Sensor.9; also elsewhere on the board
PA5: Sensor.10; also elsewhere on the board
PA6: Sensor.11; also elsewhere on the board
PA7: Sensor.12; also elsewhere on the board
PB0: Sensor.4; also elsewhere on the board

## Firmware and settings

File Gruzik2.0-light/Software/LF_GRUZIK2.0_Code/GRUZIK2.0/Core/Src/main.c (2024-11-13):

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
/* Includes ------------------------------------------------------------------*/
#include "main.h"
#include "adc.h"
#include "dma.h"
#include "tim.h"
#include "usart.h"
#include "gpio.h"

/* USER CODE BEGIN Includes */
#include "D:\SN-USER\HAL-SN-Functions\SN-functions.h"
#include "stdlib.h"
#include "stdio.h"
#include "string.h"
#include "Line_Follower.h"
#include "RingBuffer.h"
#include "SimpleParser.h"
/* USER CODE END Includes */


/* USER CODE BEGIN PV */
	/*Defines*/
	#define true 1;
	#define false 0;
	#define ENDLINE '\n'

	LineFollower_t GRUZIK;

	/*Rest of PIDR regulator*/
	int Sensors_read = 0x00000000;
	int Position;
	float Ki = 0;
	float Kr = 0;
	int P, I, D, R;
	int Last_error = 0;
	int Errors[10] = {0,0,0,0,0,0,0,0,0,0};
	int Error_sum = 0;
	int Last_end = 0;	// 0 -> Left, 1 -> Right
	int Last_idle = 0;
	float Speed_level = 1;
	int ARR = 4;
	int actives = 0;

	/*Communication*/
    char buffer[28];
    uint8_t RxData;
	RingBuffer_t RB, ReceiveBuffer;
	uint8_t ReceivedData[32];
	uint8_t ReceivedLines;

	static uint32_t low_voltage_time;
	static uint8_t low_voltage_flag = 0;

/* USER CODE END PV */

void SystemClock_Config(void);
/* USER CODE BEGIN PFP */
void PID_control();
int errors_sum (int index, int abs);
void past_errors (int error);
void forward_brake(int pos_right, int pos_left);
int QTR8_read();
void sharp_turn();
void motor_control (double pos_right, double pos_left);
void Set_Pin_Input (GPIO_TypeDef *GPIOx, uint16_t GPIO_Pin);
void Set_Pin_Output (GPIO_TypeDef *GPIOx, uint16_t GPIO_Pin);
void delay_us (uint16_t us);
/* USER CODE END PFP */

/**
  * @brief  The application entry point.
  * @retval int
  */
int main(void)
{
  /* MCU Configuration--------------------------------------------------------*/

  /* Reset of all peripherals, Initializes the Flash interface and the Systick. */
  HAL_Init();

  /* Configure the system clock */
  SystemClock_Config();

  /* Initialize all configured peripherals */
  MX_GPIO_Init();
  MX_DMA_Init();
  MX_TIM1_Init();
  MX_TIM3_Init();
  MX_TIM4_Init();
  MX_USART1_UART_Init();
  MX_USART3_UART_Init();
  MX_ADC1_Init();
  MX_TIM2_Init();
  /* USER CODE BEGIN 2 */
  /*Initial values for PID*/
  /*Start ADC with DMA measurement*/
  HAL_ADC_Start_DMA(&hadc1, (uint32_t*)&GRUZIK.Adc_Value, 1);

  	GRUZIK.Kp = 0.02;
	GRUZIK.Kd = 0.1;
	GRUZIK.Speed_offset = 0.014;

	GRUZIK.Base_speed_R = 120;
	GRUZIK.Base_speed_L = 120;
	GRUZIK.Max_speed_R = 120;
	GRUZIK.Max_speed_L = 120;

	/*Sharp turn speed*/
	GRUZIK.Sharp_bend_speed_right=-70;
	GRUZIK.Sharp_bend_speed_left=85;
	GRUZIK.Bend_speed_right=-50;
	GRUZIK.Bend_speed_left=110;

  /*Start receiving data from Blue tooth*/
   HAL_UART_Receive_IT(&huart1, &RxData, 1);

   /*Start timers and PWM on channels*/
   HAL_TIM_Base_Start_IT(&htim1);
   HAL_TIM_Base_Start(&htim2);

   HAL_TIM_PWM_Start(&htim4, TIM_CHANNEL_1);
   HAL_TIM_PWM_Start(&htim4, TIM_CHANNEL_2);
   HAL_TIM_PWM_Start(&htim4, TIM_CHANNEL_3);
   HAL_TIM_PWM_Start(&htim4, TIM_CHANNEL_4);
  /* USER CODE END 2 */

  /* Infinite loop */
  /* USER CODE BEGIN WHILE */
  while (1)
  {
    /* USER CODE END WHILE */

    /* USER CODE BEGIN 3 */
	  PID_control();

	  if(ReceivedLines > 0)
	  {
		  Parser_TakeLine(&ReceiveBuffer, ReceivedData);
		  Parser_Parse(ReceivedData,&GRUZIK);

		  ReceivedLines--;
	  }
  }
  /* USER CODE END 3 */
}

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
/* USER CODE BEGIN 4 */
void HAL_UART_RxCpltCallback(UART_HandleTypeDef *huart)
{
	if(huart->Instance == USART1)
	{
		if(RB_Write(&ReceiveBuffer, RxData) == RB_OK)
		{
			if(RxData == ENDLINE)
			{
				ReceivedLines++;
			}
		}
    	HAL_UART_Receive_IT(&huart1,&RxData, 1);
	}
}
void delay_us (uint16_t us) //Blocking function
{
	__HAL_TIM_SET_COUNTER(&htim2,0);  // set the counter value a 0
	while (__HAL_TIM_GET_COUNTER(&htim2) < us);  // wait for the counter to reach the us input in the parameter
}

void Set_Pin_Output (GPIO_TypeDef *GPIOx, uint16_t GPIO_Pin)
{
	GPIO_InitTypeDef GPIO_InitStruct = {0};
	GPIO_InitStruct.Pin = GPIO_Pin;
	GPIO_InitStruct.Mode = GPIO_MODE_OUTPUT_PP;
	GPIO_InitStruct.Speed = GPIO_SPEED_FREQ_LOW;
	HAL_GPIO_Init(GPIOx, &GPIO_InitStruct);
}

void Set_Pin_Input (GPIO_TypeDef *GPIOx, uint16_t GPIO_Pin)
{
	GPIO_InitTypeDef GPIO_InitStruct = {0};
	GPIO_InitStruct.Pin = GPIO_Pin;
	GPIO_InitStruct.Mode = GPIO_MODE_INPUT;
	GPIO_InitStruct.Pull = GPIO_PULLUP;
	HAL_GPIO_Init(GPIOx, &GPIO_InitStruct);
}


void motor_control (double pos_right, double pos_left)
{
	if (pos_left < 0 )
	{
		__HAL_TIM_SET_COMPARE (&htim4, TIM_CHANNEL_2, (uint32_t)((ARR*pos_left*-1) * GRUZIK.Speed_level));
		HAL_GPIO_WritePin(GPIOB, GPIO_PIN_15, GPIO_PIN_SET);
		HAL_GPIO_WritePin(GPIOB, GPIO_PIN_14, GPIO_PIN_RESET);
	}
	else
	{
		__HAL_TIM_SET_COMPARE (&htim4, TIM_CHANNEL_2, (uint32_t)((ARR*pos_left) * GRUZIK.Speed_level));
		HAL_GPIO_WritePin(GPIOB, GPIO_PIN_15, GPIO_PIN_RESET);
		HAL_GPIO_WritePin(GPIOB, GPIO_PIN_14, GPIO_PIN_SET);
	}
	if (pos_right < 0 )
	{
		__HAL_TIM_SET_COMPARE (&htim4, TIM_CHANNEL_4, (uint32_t)((ARR*pos_right* -1) * GRUZIK.Speed_level));
		HAL_GPIO_WritePin(GPIOB, GPIO_PIN_5, GPIO_PIN_SET);
		HAL_GPIO_WritePin(GPIOB, GPIO_PIN_4, GPIO_PIN_RESET);
	}
	else
	{
		__HAL_TIM_SET_COMPARE (&htim4, TIM_CHANNEL_4, (uint32_t)((ARR*pos_right) * GRUZIK.Speed_level));
		HAL_GPIO_WritePin(GPIOB, GPIO_PIN_5, GPIO_PIN_RESET);
		HAL_GPIO_WritePin(GPIOB, GPIO_PIN_4, GPIO_PIN_SET);
	}
}


void sharp_turn ()
{

	if (Last_idle < 25)
	{
		if (Last_end == 1)
			motor_control(GRUZIK.Sharp_bend_speed_right, GRUZIK.Sharp_bend_speed_left);
		else
			motor_control(GRUZIK.Sharp_bend_speed_left, GRUZIK.Sharp_bend_speed_right);
	}
	else
	{
		if (Last_end == 1)
			motor_control(GRUZIK.Bend_speed_right, GRUZIK.Bend_speed_left);
		else
			motor_control(GRUZIK.Bend_speed_left, GRUZIK.Bend_speed_right);
	}
}
int QTR8_read ()
{
	HAL_GPIO_WritePin(LEDON_GPIO_Port, LEDON_Pin, 1);

	Set_Pin_Output(SENSOR1_GPIO_Port, SENSOR1_Pin);
	Set_Pin_Output(SENSOR2_GPIO_Port, SENSOR2_Pin);
	Set_Pin_Output(SENSOR3_GPIO_Port, SENSOR3_Pin);
	Set_Pin_Output(SENSOR4_GPIO_Port, SENSOR4_Pin);
	Set_Pin_Output(SENSOR5_GPIO_Port, SENSOR5_Pin);
	Set_Pin_Output(SENSOR6_GPIO_Port, SENSOR6_Pin);
	Set_Pin_Output(SENSOR7_GPIO_Port, SENSOR7_Pin);
	Set_Pin_Output(SENSOR8_GPIO_Port, SENSOR8_Pin);

	HAL_GPIO_WritePin (SENSOR1_GPIO_Port, SENSOR1_Pin, 1);
	HAL_GPIO_WritePin (SENSOR2_GPIO_Port, SENSOR2_Pin, 1);
	HAL_GPIO_WritePin (SENSOR3_GPIO_Port, SENSOR3_Pin, 1);
	HAL_GPIO_WritePin (SENSOR4_GPIO_Port, SENSOR4_Pin, 1);
	HAL_GPIO_WritePin (SENSOR5_GPIO_Port, SENSOR5_Pin, 1);
	HAL_GPIO_WritePin (SENSOR6_GPIO_Port, SENSOR6_Pin, 1);
	HAL_GPIO_WritePin (SENSOR7_GPIO_Port, SENSOR7_Pin, 1);
	HAL_GPIO_WritePin (SENSOR8_GPIO_Port, SENSOR8_Pin, 1);

	delay_us(10);

	Set_Pin_Input(SENSOR1_GPIO_Port, SENSOR1_Pin);
	Set_Pin_Input(SENSOR2_GPIO_Port, SENSOR2_Pin);
	Set_Pin_Input(SENSOR3_GPIO_Port, SENSOR3_Pin);
	Set_Pin_Input(SENSOR4_GPIO_Port, SENSOR4_Pin);
	Set_Pin_Input(SENSOR5_GPIO_Port, SENSOR5_Pin);
	Set_Pin_Input(SENSOR6_GPIO_Port, SENSOR6_Pin);
	Set_Pin_Input(SENSOR7_GPIO_Port, SENSOR7_Pin);
	Set_Pin_Input(SENSOR8_GPIO_Port, SENSOR8_Pin);

	// Threshold
	 delay_us(4500);
	 	 	 //!!! FOR SENSOR TESTING ONLY !!!//

//	 uint8_t sensory[8];
//	 sensory[0] = HAL_GPIO_ReadPin(SENSOR1_GPIO_Port, SENSOR1_Pin);
//	 sensory[1] = HAL_GPIO_ReadPin(SENSOR2_GPIO_Port, SENSOR2_Pin);
//	 sensory[2] = HAL_GPIO_ReadPin(SENSOR3_GPIO_Port, SENSOR3_Pin);
//	 sensory[3] = HAL_GPIO_ReadPin(SENSOR4_GPIO_Port, SENSOR4_Pin);
//	 sensory[4] = HAL_GPIO_ReadPin(SENSOR5_GPIO_Port, SENSOR5_Pin);
//	 sensory[5] = HAL_GPIO_ReadPin(SENSOR6_GPIO_Port, SENSOR6_Pin);
//	 sensory[6] = HAL_GPIO_ReadPin(SENSOR7_GPIO_Port, SENSOR7_Pin);
//	 sensory[7] = HAL_GPIO_ReadPin(SENSOR8_GPIO_Port, SENSOR8_Pin);
//	 uint8_t Message[64];
//	 sprintf((char*)Message,"S1: %d S2: %d S3: %d S4: %d S5: %d S6: %d S7: %d S8: %d\n\r", sensory[0],sensory[1],sensory[2],sensory[3],sensory[4],sensory[5],sensory[6],sensory[7]);
//	 HAL_UART_Transmit(&huart3, Message, strlen((char*)Message), 100);

	Sensors_read = 0x00000000;
	int pos = 0;
  int active = 0;

	if (HAL_GPIO_ReadPin(SENSOR1_GPIO_Port, SENSOR1_Pin)) {
		Sensors_read |= 0x00000001;
		pos += 1000;//1000
    active++;
		Last_end = 1;
	}
	if (HAL_GPIO_ReadPin(SENSOR2_GPIO_Port, SENSOR2_Pin)) {
		Sensors_read |= 0x00000010;
		pos += 2000;//2000
    active++;
  }
	if (HAL_GPIO_ReadPin(SENSOR3_GPIO_Port, SENSOR3_Pin)) {
		Sensors_read |= 0x00000100;
		pos += 3000;//3000
    active++;
  }
	if (HAL_GPIO_ReadPin(SENSOR4_GPIO_Port, SENSOR4_Pin)) {
		Sensors_read |= 0x00001000;
		pos += 4000;//4000
    active++;
  }
	if (HAL_GPIO_ReadPin(SENSOR5_GPIO_Port, SENSOR5_Pin)) {
		Sensors_read |= 0x00010000;
		pos += 5000;//5000
    active++;
  }
	if (HAL_GPIO_ReadPin(SENSOR6_GPIO_Port, SENSOR6_Pin)) {
		Sensors_read |= 0x00100000;
		pos += 6000;//6000
    active++;
  }
	if (HAL_GPIO_ReadPin(SENSOR7_GPIO_Port, SENSOR7_Pin)) {
		Sensors_read |= 0x01000000;
		pos += 7000;//7000
    active++;
  }
	if (HAL_GPIO_ReadPin(SENSOR8_GPIO_Port, SENSOR8_Pin)) {
		Sensors_read |= 0x10000000;
		pos += 8000;//8000
    active++;
		Last_end = 0;
  }

  HAL_GPIO_WritePin(LEDON_GPIO_Port, LEDON_Pin, 0);

  actives = active;
	Position = pos/active;

	if (actives == 0)
		Last_idle++;
	else
		Last_idle = 0;

	return pos/active;
}


void forward_brake(int pos_right, int pos_left)
{
	if (actives == 0)
		sharp_turn();
	else
	  motor_control(pos_right, pos_left);
}

void past_errors (int error)
{
  for (int i = 9; i > 0; i--)
      Errors[i] = Errors[i-1];
  Errors[0] = error;
}

int errors_sum (int index, int abs)
{
  int sum = 0;
  for (int i = 0; i < index; i++)
  {
    if (abs == 1 && Errors[i] < 0)
      sum += -Errors[i];
    else
      sum += Errors[i];
  }
  return sum;
}

void PID_control()
{
  uint16_t position = QTR8_read();
  int error = 4500 - position;
  past_errors(error);

  P = error;
  I = errors_sum(5, 0);
  D = error - Last_error;
  R = errors_sum(5, 1);
  Last_error = error;

  int motorspeed = P*GRUZIK.Kp + I*Ki + D*GRUZIK.Kd;

  int motorspeedl = GRUZIK.Base_speed_L + motorspeed - R*Kr;
  int motorspeedr = GRUZIK.Base_speed_R - motorspeed - R*Kr;

  if (motorspeedl > GRUZIK.Max_speed_L)
    motorspeedl = GRUZIK.Max_speed_L;
  if (motorspeedr > GRUZIK.Max_speed_R)
    motorspeedr = GRUZIK.Max_speed_R;

	forward_brake(motorspeedr, motorspeedl);
}
/* USER CODE END 4 */
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


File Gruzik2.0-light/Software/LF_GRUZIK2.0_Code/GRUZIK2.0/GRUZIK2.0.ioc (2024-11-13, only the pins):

Mcu.UserName=STM32F103C8Tx
PA0-WKUP.GPIO_Label=SENSOR8
PA0-WKUP.Signal=GPIO_Output
PA1.GPIO_Label=SENSOR7
PA1.Signal=GPIO_Output
PA10.Signal=USART1_RX
PA13.Signal=SYS_JTMS-SWDIO
PA14.Signal=SYS_JTCK-SWCLK
PA2.GPIO_Label=SENSOR6
PA2.Signal=GPIO_Output
PA3.GPIO_Label=SENSOR5
PA3.Signal=GPIO_Output
PA4.GPIO_Label=SENSOR4
PA4.Signal=GPIO_Output
PA5.GPIO_Label=SENSOR3
PA5.Signal=GPIO_Output
PA6.GPIO_Label=SENSOR2
PA6.Signal=GPIO_Output
PA7.GPIO_Label=SENSOR1
PA7.Signal=GPIO_Output
PA9.Signal=USART1_TX
PB0.GPIO_Label=LEDON
PB0.Signal=GPIO_Output
PB1.Signal=ADCx_IN9
PB10.Signal=USART3_TX
PB11.Signal=USART3_RX
PB14.GPIO_Label=BIN1L
PB14.Signal=GPIO_Output
PB15.GPIO_Label=BIN1R
PB15.Signal=GPIO_Output
PB4.GPIO_Label=AIN2L
PB4.Signal=GPIO_Output
PB5.GPIO_Label=AIN1R
PB5.Signal=GPIO_Output
PB6.Signal=GPIO_Output
PB7.Signal=S_TIM4_CH2
PB8.Signal=S_TIM4_CH3
PB9.Signal=S_TIM4_CH4
PC13-TAMPER-RTC.GPIO_Label=LD
PC13-TAMPER-RTC.Signal=GPIO_Output
PD0-OSC_IN.Signal=RCC_OSC_IN
PD1-OSC_OUT.Signal=RCC_OSC_OUT

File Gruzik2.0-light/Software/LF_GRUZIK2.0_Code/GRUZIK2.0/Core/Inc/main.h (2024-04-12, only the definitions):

#define LD_Pin GPIO_PIN_13
#define LD_GPIO_Port GPIOC
#define SENSOR8_Pin GPIO_PIN_0
#define SENSOR8_GPIO_Port GPIOA
#define SENSOR7_Pin GPIO_PIN_1
#define SENSOR7_GPIO_Port GPIOA
#define SENSOR6_Pin GPIO_PIN_2
#define SENSOR6_GPIO_Port GPIOA
#define SENSOR5_Pin GPIO_PIN_3
#define SENSOR5_GPIO_Port GPIOA
#define SENSOR4_Pin GPIO_PIN_4
#define SENSOR4_GPIO_Port GPIOA
#define SENSOR3_Pin GPIO_PIN_5
#define SENSOR3_GPIO_Port GPIOA
#define SENSOR2_Pin GPIO_PIN_6
#define SENSOR2_GPIO_Port GPIOA
#define SENSOR1_Pin GPIO_PIN_7
#define SENSOR1_GPIO_Port GPIOA
#define LEDON_Pin GPIO_PIN_0
#define LEDON_GPIO_Port GPIOB
#define BIN1L_Pin GPIO_PIN_14
#define BIN1L_GPIO_Port GPIOB
#define BIN1R_Pin GPIO_PIN_15
#define BIN1R_GPIO_Port GPIOB
#define AIN2L_Pin GPIO_PIN_4
#define AIN2L_GPIO_Port GPIOB
#define AIN1R_Pin GPIO_PIN_5
#define AIN1R_GPIO_Port GPIOB

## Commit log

2023-12-21 1.0
    Hardware done
    [Frame_thinner.stl, GRUZIK2.0-BOM.xlsx, GRUZIK2.0_Frame_Part.stl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]
2023-12-22 1.1
    Added ADC and constant motor speed
2024-03-28 New Sensor
    [Qtr-8-SN.csv, Qtr-8-SN.kicad_pcb, Qtr-8-SN.kicad_sch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]
2024-03-28 1.9.2
    new sensor added
    [koszty.xlsx]
2024-04-12 2.0.1
    New sensor frame and upgraded software
    [Frame_1.stl, Frame_2.stl, Gruzik2.0 v16.f3d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]
2024-04-21 2.1.4
    changed sensor mount
    [Frame_1.stl, Frame_2.stl, LF_wheel.stl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]
2024-07-09 2.1.5
    Mother board rev2
    [GRUZIK2.0-BOM.xlsx, Gruzik2.0.csv, Gruzik2.0.kicad_pcb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]
2024-07-12 2.1.6
    motherboard rev 2 update
    [Gruzik2.0.kicad_pcb]
2024-10-17 2.1.8
    Added new rims & better main board :+1:
    [Gruzik2.0-B_Cu.gbl, Gruzik2.0-B_Mask.gbs, Gruzik2.0-B_Paste.gbp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]
2024-11-13 2.3.1
    Added new features like new motor mounts new modes etc

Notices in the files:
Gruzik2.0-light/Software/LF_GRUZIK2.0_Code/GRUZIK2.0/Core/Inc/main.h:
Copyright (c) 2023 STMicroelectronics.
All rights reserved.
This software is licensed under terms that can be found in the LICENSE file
